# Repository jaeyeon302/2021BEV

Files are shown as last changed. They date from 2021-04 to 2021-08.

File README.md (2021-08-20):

# 2021BEV 
2021 Bachelor's degree Graduation Project, Battery Electric Vehicle  
Department of Electrical and Conputer Engineering, Seoul National University  

- Advisor : [Professor Seung-ki Sul](http://eepel.snu.ac.kr/wordpress/professor/)

## Demo Video

### [Test driving 1 : Seoul National University Campus Road (youtube video)](https://youtu.be/YFAJCFfAURw)
- Path length : 4.06Km
- Maximum slope : 7%
- Maximum speed : 30.5km/h

### [Test driving 2 : Cooling Performance test (youtube video)](https://youtu.be/0JFbmtatzrk)
- place : Seoul National University Electric Power Research Institute Parking Lot
- settled down at 44 celcius degree
- continuous maximum q-axis current (30A)

## What I made

### Inverter
- 4 layer PCB artwork (1oz 2oz 2oz 1oz) 
- Used IPM([NFAL5065L4B](https://kr.mouser.com/datasheet/2/308/1/NFAL5065L4B_D-2317681.pdf)) as the power IGBT switch
- Electrically isolated control board area from the High Power Area including IPM and DC link

### DSP - controller
- TMS320F2839D Launchpad
- Built the q-axis current regulator(PI controller with feedforward) from the scratch including resgister setting(ePWM, eCAP, GPIO, Clock, Timer)
- Implemented rotor position and speed observer to estimate right position of rotor for DQ transformation and feedforward control

## Future work
- Robust control algorithm to prevent sudden current peak from the disturbance.   
  Since there is no mechanical damper between ground and motor wheel, Bumpy road surface directly affects the controller's performance
- Hall sensor type curernt sensor removal. because the IPM already provides extra ports to measure the phase current using small register.

## Photos
- [Bicycle Photo](https://photos.app.goo.gl/71CFiTBS6PbSPb559)
- [Inverter Photo](https://photos.app.goo.gl/JQpmmjE8fstSpoiK7)

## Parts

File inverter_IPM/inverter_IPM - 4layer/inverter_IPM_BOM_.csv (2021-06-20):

Source: | G:\???滊澕?措笇\0. parkjani2 DRIVE\彀胳棳 PROJECT\?勲?濏姼\2021 臁疙攧\2021_臁疙攧_workspace(shared)\PCB - inverter\inverter_IPM\inverter_IPM - 4layer\inverter_IPM.sch
Date: | 2021-03-22 ?れ爠 11:46:58
Tool: | Eeschema (5.1.8)-1
Generator: | C:\Program Files\KiCad\bin\scripting\plugins/bom_csv_grouped_by_value_with_fp.py
Component Count: | 144
Ref | Qnty | Value | Cmp name | man# | Footprint | Description | Vendor
C1, C5, C17, C24, C33, C37, C38, C41, C44, C47, C48, C51, C53, C56, C61, | 15 | 1nF/2KV | C_Small | C1206C102KGRACTU | Capacitor_SMD:C_1206_3216Metric_Pad1.33x1.80mm_HandSolder | Unpolarized capacitor, small symbol
C2, C58, | 2 | 330uF/100V | CP1_Small | UVR2A331MHD | Capacitor_THT:CP_Radial_D12.5mm_P5.00mm | Polarized capacitor, small US symbol
C3, C59, | 2 | 1uF | C_Small | C3216X7R2A105K160AA | Capacitor_SMD:C_1206_3216Metric_Pad1.33x1.80mm_HandSolder | Unpolarized capacitor, small symbol
C4, C49, C62, C64, | 4 | 10uF/25V | C_Small | TMK212BC6106KG-T | Capacitor_SMD:C_0805_2012Metric_Pad1.18x1.45mm_HandSolder | Unpolarized capacitor, small symbol
C6, | 1 | 2.2mF | CP1 | SLPX222M100E3P3 | Capacitor_THT:CP_Radial_D30.0mm_P10.00mm_SnapIn | Polarized capacitor, US symbol
C7, C8, | 2 | 100uF/16V | CP1_Small | F931C107MCC | Capacitor_Tantalum_SMD:CP_EIA-6032-20_AVX-F_Pad2.25x2.35mm_HandSolder | Polarized capacitor, small US symbol
C9, C16, C18, C19, C20, C21, C23, C25, C27, C28, C29, C30, C32, C34, C36, C40, C43, C52, C54, C63, | 20 | 100nF | C_Small | HMF316B7104KLHT | Capacitor_SMD:C_1206_3216Metric_Pad1.33x1.80mm_HandSolder | Unpolarized capacitor, small symbol
C10, | 1 | 8.2pF | C_Small | C1206C829D5GACTU | Capacitor_SMD:C_1206_3216Metric_Pad1.33x1.80mm_HandSolder | Unpolarized capacitor, small symbol
C11, | 1 | 47uF | CP1_Small | A768KS476M1JLAE031 | Capacitor_SMD:CP_Elec_8x11.9 | Polarized capacitor, small US symbol
C12, C13, C14, | 3 | 2.2uF | C_Small | HMK325BJ225KM-P | Capacitor_SMD:C_1210_3225Metric_Pad1.33x2.70mm_HandSolder | Unpolarized capacitor, small symbol
C15, | 1 | 750pF | C_Small | C1206C751J5GACTU | Capacitor_SMD:C_1206_3216Metric_Pad1.33x1.80mm_HandSolder | Unpolarized capacitor, small symbol
C22, C31, C35, C57, C60, | 5 | 10uF/100V | C_Small | GRM32EC72A106KE05L | Capacitor_SMD:C_1210_3225Metric_Pad1.33x2.70mm_HandSolder | Unpolarized capacitor, small symbol
C26, C42, | 2 | 100uF/100V | CP1_Small | EEU-FR2A101 | Capacitor_THT:CP_Radial_D10.0mm_P5.00mm | Polarized capacitor, small US symbol
C39, | 1 | 1nF/2kV | C_Small | C1206C102KGRACTU | Capacitor_SMD:C_1206_3216Metric_Pad1.33x1.80mm_HandSolder | Unpolarized capacitor, small symbol
C45, | 1 | 10nF | C_Small | GRM2195C1H103JA01D | Capacitor_SMD:C_0805_2012Metric_Pad1.18x1.45mm_HandSolder | Unpolarized capacitor, small symbol
C46, C50, C55, | 3 | 2.2pF | C_Small | VJ0805A2R2BXACW1BC | Capacitor_SMD:C_0805_2012Metric_Pad1.18x1.45mm_HandSolder | Unpolarized capacitor, small symbol
D1, | 1 | VFT2080S-E3/4W | D_Schottky_AKA | VFT2080S-E3/4W | Package_TO_SOT_THT:TO-220-3_Vertical | Schottky diode, anode on pins 1 and 3
D2, D3, D4, D5, | 4 | SMAZ22-TP | D_Zener_Small | SMAZ22-TP | Diode_SMD:D_SMA_Handsoldering | Zener diode, small symbol
J1, | 1 | PinHeader01x03 | Conn_01x03 | PinHeader01x03 | Connector_PinHeader_2.54mm:PinHeader_1x03_P2.54mm_Vertical | Generic connector, single row, 01x03, script generated (kicad-library-utils/schlib/autogen/connector/)
J2, J3, | 2 | BR-1300C-6P | Conn_01x06 | BR-1300C-6P | j_terminal:BR-1300C-6P | Generic connector, single row, 01x06, script generated (kicad-library-utils/schlib/autogen/connector/)
J4, | 1 | MOLEX01x03 | Conn_01x03 | MOLEX_5267-03 | Connector_Molex:Molex_SPOX_5267-03A_1x03_P2.50mm_Vertical | Generic connector, single row, 01x03, script generated (kicad-library-utils/schlib/autogen/connector/)
J5, | 1 | MOLEX01x05 | Conn_01x05 | MOLEX_5267-05 | Connector_Molex:Molex_SPOX_5267-05A_1x05_P2.50mm_Vertical | Generic connector, single row, 01x05, script generated (kicad-library-utils/schlib/autogen/connector/)
J6, J8, J9, | 3 | SMA | Conn_Coaxial | SMA | Connector_Coaxial:SMA_Amphenol_132203-12_Horizontal | coaxial connector (BNC, SMA, SMB, SMC, Cinch/RCA, ...)
J7, | 1 | JST8P | Conn_01x08 | JST8P | Connector_JST:JST_VH_B8P-VH-B_1x08_P3.96mm_Vertical | Generic connector, single row, 01x08, script generated (kicad-library-utils/schlib/autogen/connector/)
J10, | 1 | MOLEX_01X05 | Conn_01x05 | molex-01x05 | Connector_Molex:Molex_SPOX_5267-05A_1x05_P2.50mm_Vertical | Generic connector, single row, 01x05, script generated (kicad-library-utils/schlib/autogen/connector/)
J11, | 1 | Hirose_HIF3BA_30PA_2.54DSA | Conn_02x15_Odd_Even |  | Connector_PinSocket_2.54mm:PinSocket_2x15_P2.54mm_Vertical | Generic connector, double row, 02x15, odd/even pin numbering scheme (row 1 odd numbers, row 2 even numbers), script generated (kicad-library-utils/schlib/autogen/connector/)
J12, | 1 | PinHeader01x02 | Conn_01x02 | pinheader 01x02 | Connector_PinHeader_2.54mm:PinHeader_1x02_P2.54mm_Vertical | Generic connector, single row, 01x02, script generated (kicad-library-utils/schlib/autogen/connector/)
J13, | 1 | HIF3 2X5 | Conn_02x05_Odd_Even | HIF3 2X5 | Connector_PinHeader_2.54mm:PinHeader_2x05_P2.54mm_Vertical | Generic connector, double row, 02x05, odd/even pin numbering scheme (row 1 odd numbers, row 2 even numbers), script generated (kicad-library-utils/schlib/autogen/connector/)
K1, | 1 | ADJH21012 | ADJH21012 | ADJH21012 | j_power_switch:Panasonic-ADJH21012-MFG | ADJH21012
L1, L3, | 2 | 4.7uH | L_Small | NRS5024T4R7MMGJV | Inductor_SMD:L_Taiyo-Yuden_NR-50xx | Inductor, small symbol
L2, | 1 | 15uH, Irms>5A | L | IHLP6767GZER150M01 | Inductor_SMD:L_Vishay_IHLP-6767 | Inductor
R1, | 1 | 442k | R_Small | HV732BTTD4423F | Resistor_SMD:R_1206_3216Metric_Pad1.30x1.75mm_HandSolder | Resistor, small symbol
R2, | 1 | 90.9k | R_Small | CRCW121090K9FKEA | Resistor_SMD:R_1210_3225Metric_Pad1.30x2.65mm_HandSolder | Resistor, small symbol
R3, | 1 | 215k | R_Small | CRCW1206215KFKEA | Resistor_SMD:R_1206_3216Metric_Pad1.30x1.75mm_HandSolder | Resistor, small symbol
R4, | 1 | 205k | R_Small | CRCW1206205KFKEA | Resistor_SMD:R_1206_3216Metric_Pad1.30x1.75mm_HandSolder | Resistor, small symbol
R5, | 1 | 44.2k | R_Small | ERA-8AEB4422V | Resistor_SMD:R_1206_3216Metric_Pad1.30x1.75mm_HandSolder | Resistor, small symbol
R6, | 1 | 12.1k | R_Small | ERA-8AEB1212V | Resistor_SMD:R_1206_3216Metric_Pad1.30x1.75mm_HandSolder | Resistor, small symbol
R7, R11, R15, R17, R20, R22, R23, | 7 | 100 | R_Small | CHP0805AFX-1000ELF | Resistor_SMD:R_0805_2012Metric_Pad1.20x1.40mm_HandSolder | Resistor, small symbol
R8, R9, R10, R12, R13, R14, R19, R34, R35, R36, R37, R38, R39, | 13 | 1k | R_Small | CMP2010AFX-1001ELF | Resistor_SMD:R_2010_5025Metric_Pad1.40x2.65mm_HandSolder | Resistor, small symbol
R16, | 1 | 5k | R_Small | CRCW08055K00FKTA | Resistor_SMD:R_0805_2012Metric_Pad1.20x1.40mm_HandSolder | Resistor, small symbol
R18, | 1 | 24 | R_Small | RK73H2ATTD24R0F | Resistor_SMD:R_0805_2012Metric_Pad1.20x1.40mm_HandSolder | Resistor, small symbol
R21, | 1 | 249 | R_Small | RK73H2ATTD2490F | Resistor_SMD:R_0805_2012Metric_Pad1.20x1.40mm_HandSolder | Resistor, small symbol
R24, R27, R28, R31, | 4 | 24k | R_Small | CR1206-JW-243ELF | Resistor_SMD:R_1206_3216Metric_Pad1.30x1.75mm_HandSolder | Resistor, small symbol
R25, R26, R29, R30, | 4 | 12k | R_Small | CRCW120612K0FKEAC | Resistor_SMD:R_1206_3216Metric_Pad1.30x1.75mm_HandSolder | Resistor, small symbol
R32, | 1 | 1M | R_Small | ERA-8AED105V | Resistor_SMD:R_1206_3216Metric_Pad1.30x1.75mm_HandSolder | Resistor, small symbol
R33, | 1 | 68k | R_Small | CRCW120668K0FKEAHP | Resistor_SMD:R_1206_3216Metric_Pad1.30x1.75mm_HandSolder | Resistor, small symbol
S1, | 1 | EG2219 | EG2219 | EG2219 | j_switch:SW_EG2219
U1, | 1 | PDQE10-Q48-S5-D | PDQE10-Q48-S5-D | PDQE10-Q48-S5-D | PDQE10:CONV_PDQE10-Q48-S5-D
U2, | 1 | SPX1587AT-3.3 | AZ1117-5.0 | SPX1587AT-3.3 | Package_TO_SOT_SMD:TO-263-3_TabPin4 | 1A 20V Fixed LDO Linear Regulator, 5.0V, SOT-89/SOT-223/TO-220/TO-252/TO-263
U3, | 1 | LAUNCHXL_F28379D | LAUNCHXL_F28379D | LAUNCHPAD_F28379D | j_modules:LAUNCHXL_F28379D
U4, | 1 | TPS54560BDDA | TPS54560BDDA | TPS54560BDDA | j_regulator_switching:NOPB
U5, | 1 | NFAL5065L4B-New_Library | NFAL5065L4B-New_Library | NFAL5065L4B | j_IPM:NFAL5065L4B
U6, U7, U8, U10, U11, U12, U13, | 7 | TLP2748 | TLP2748 | TLP2748 | Package_SO:SO-6L_10x3.84mm_P1.27mm | 10-Mbps inverting photocouple,5 kVrms, 4.5 - 30 Vdd, push-pull output, SO-6L
U9, | 1 | PDQE10-Q48-D15-D | PDQE10-Q48-D15-D | PDQE10-Q48-D15-D | PDQE10:CONV_PDQE10-Q48-D15-D
U14, U16, | 2 | LM358 | LM358 | LM358 | Package_SO:SO-8_3.9x4.9mm_P1.27mm | opamp
U15, U17, U18, | 3 | wcs1800 | wcs1800 | wcs1800 | j_current_sensor:wcs1x00-xxxx

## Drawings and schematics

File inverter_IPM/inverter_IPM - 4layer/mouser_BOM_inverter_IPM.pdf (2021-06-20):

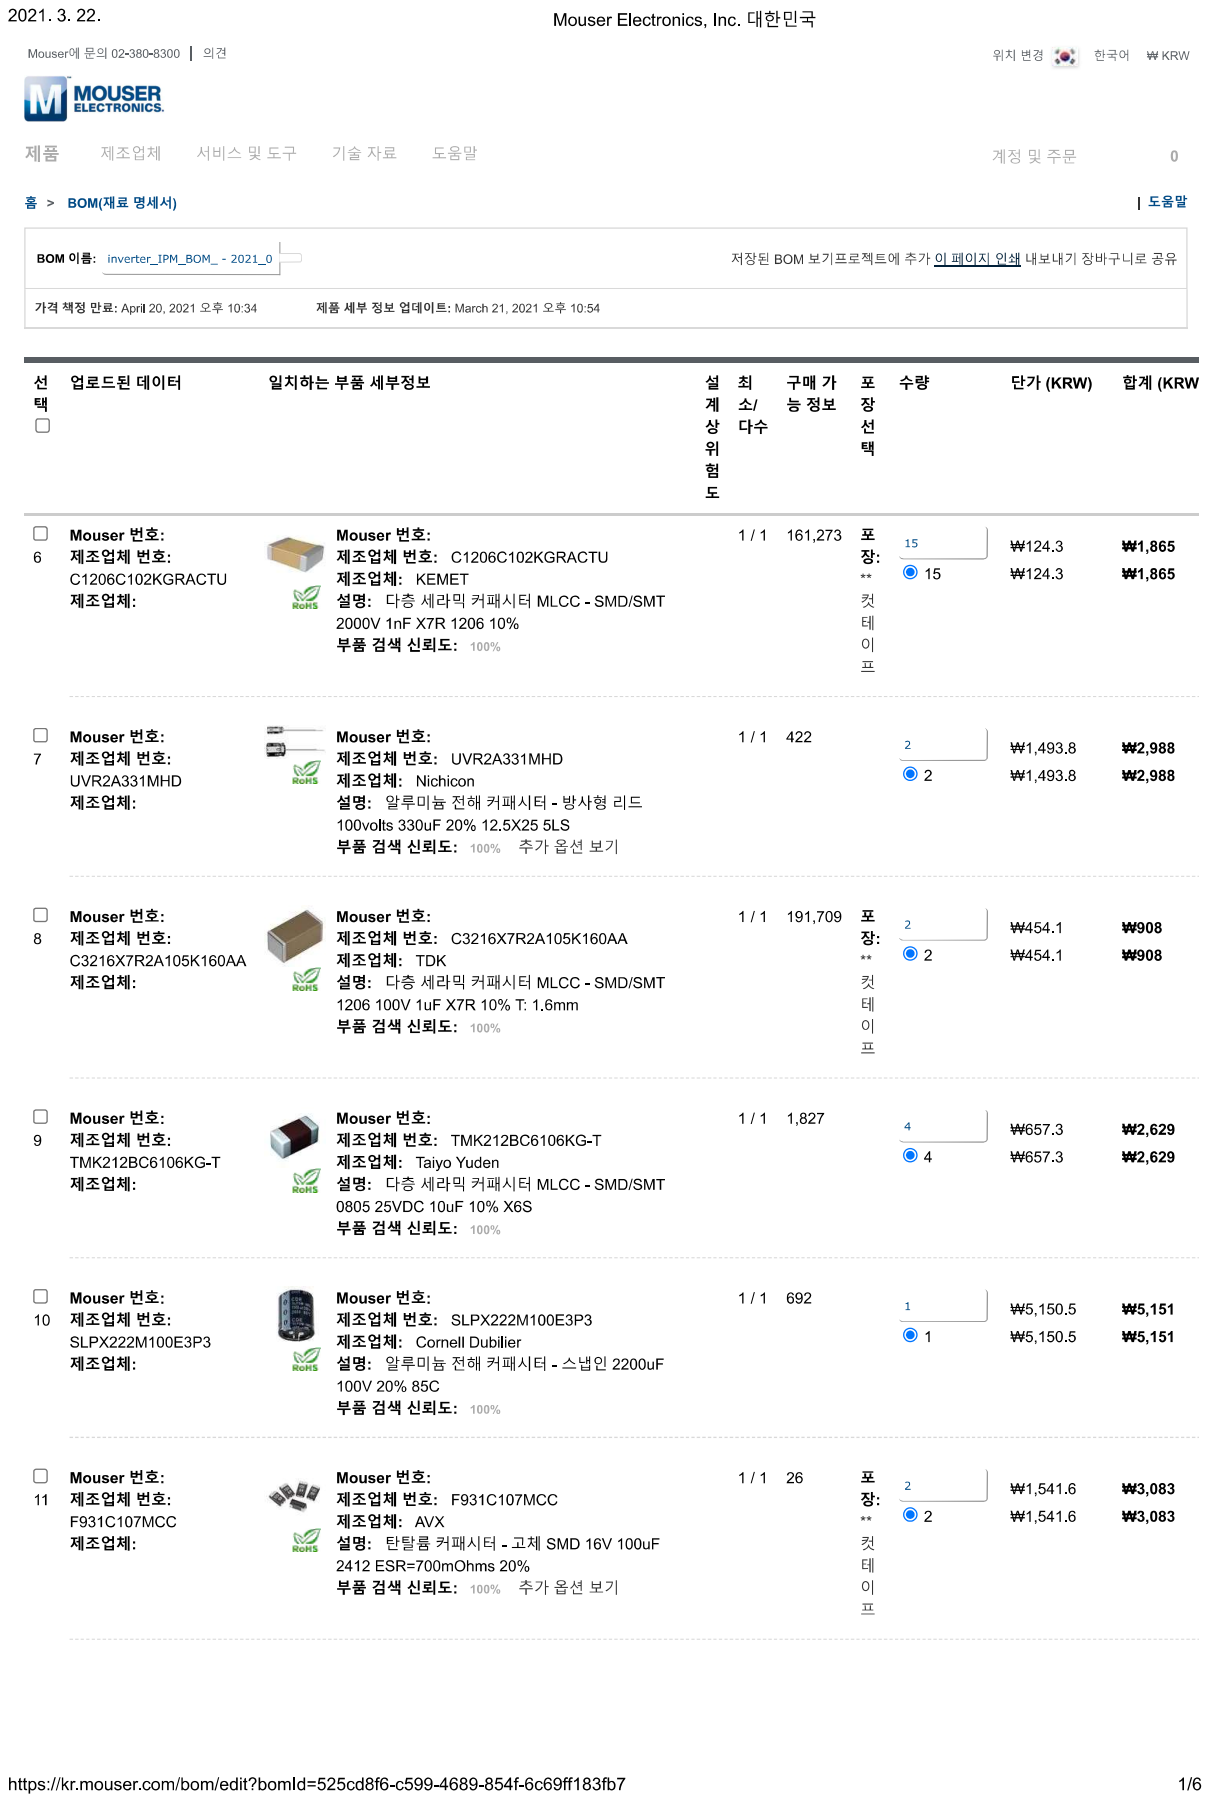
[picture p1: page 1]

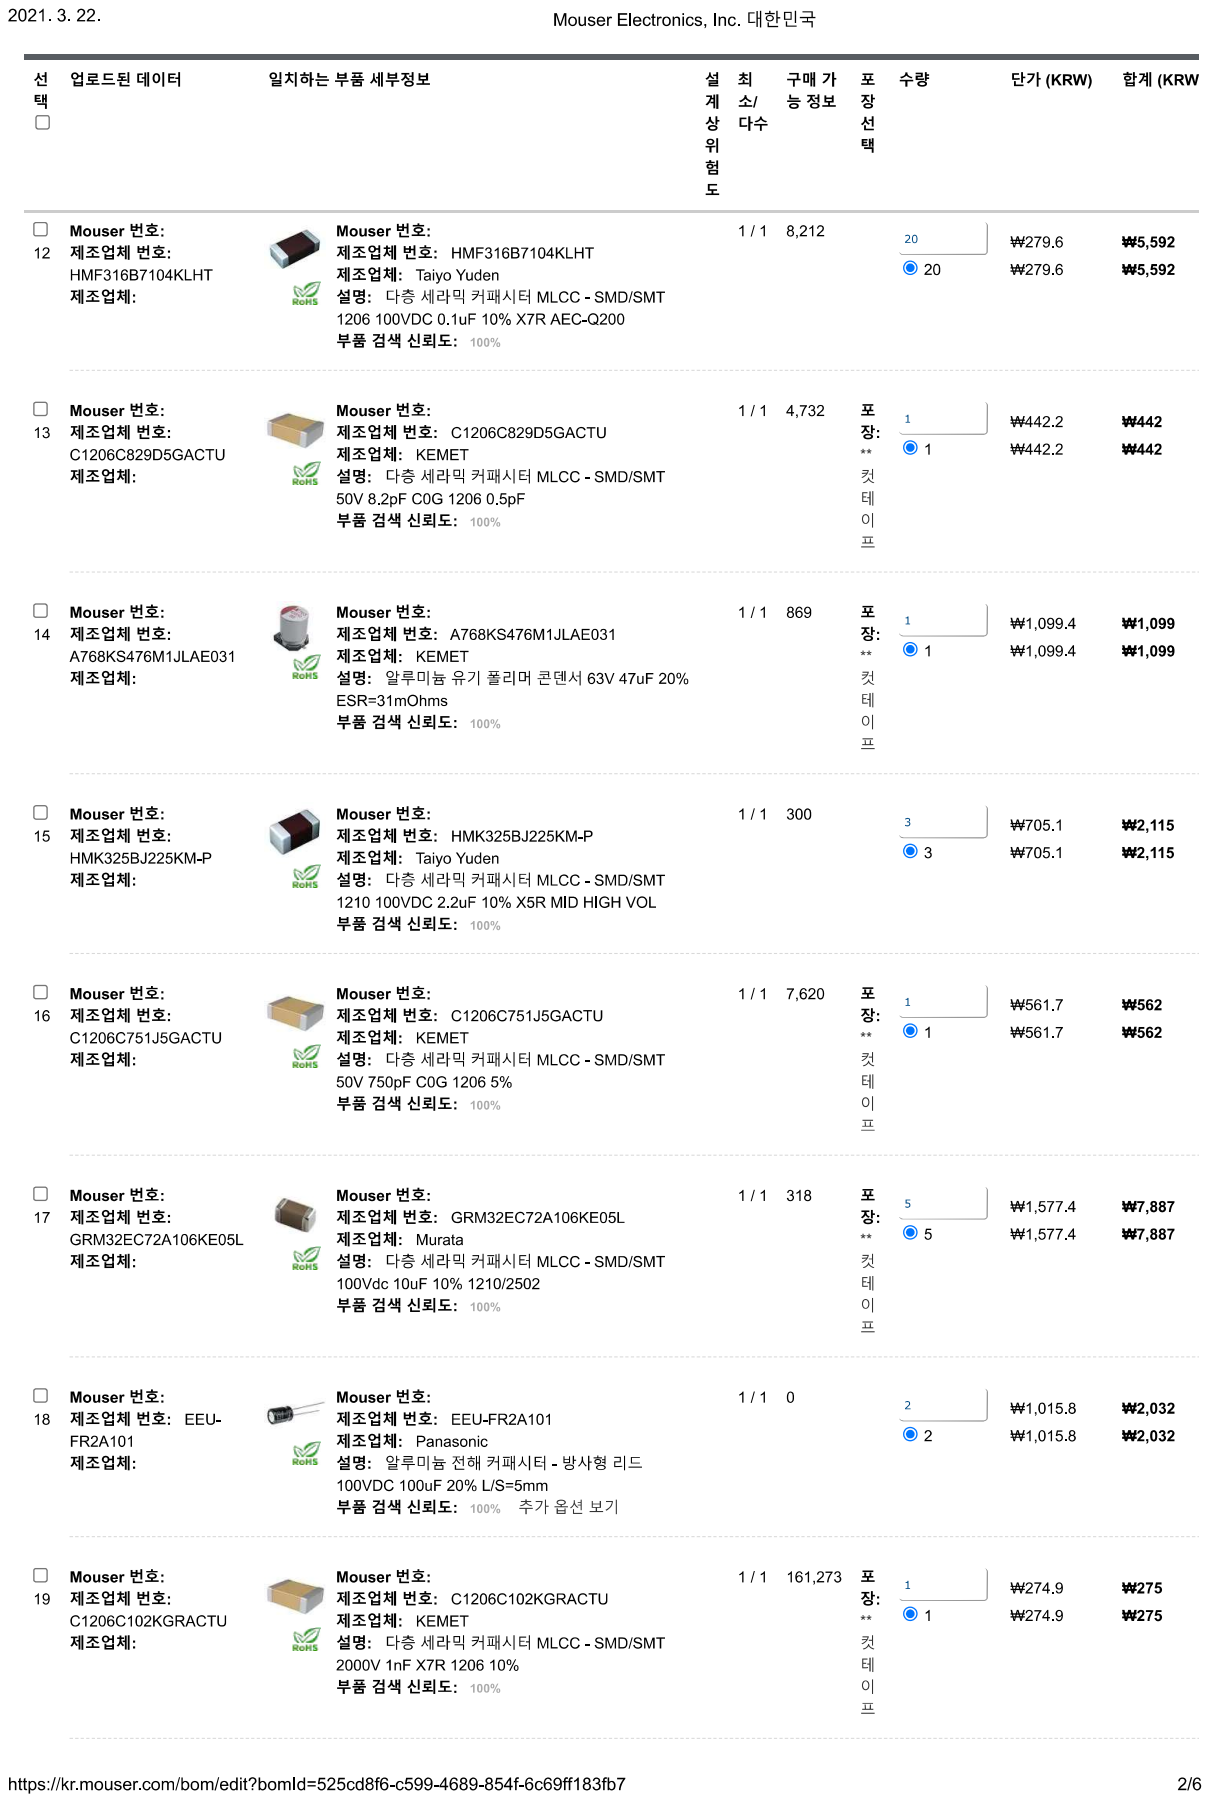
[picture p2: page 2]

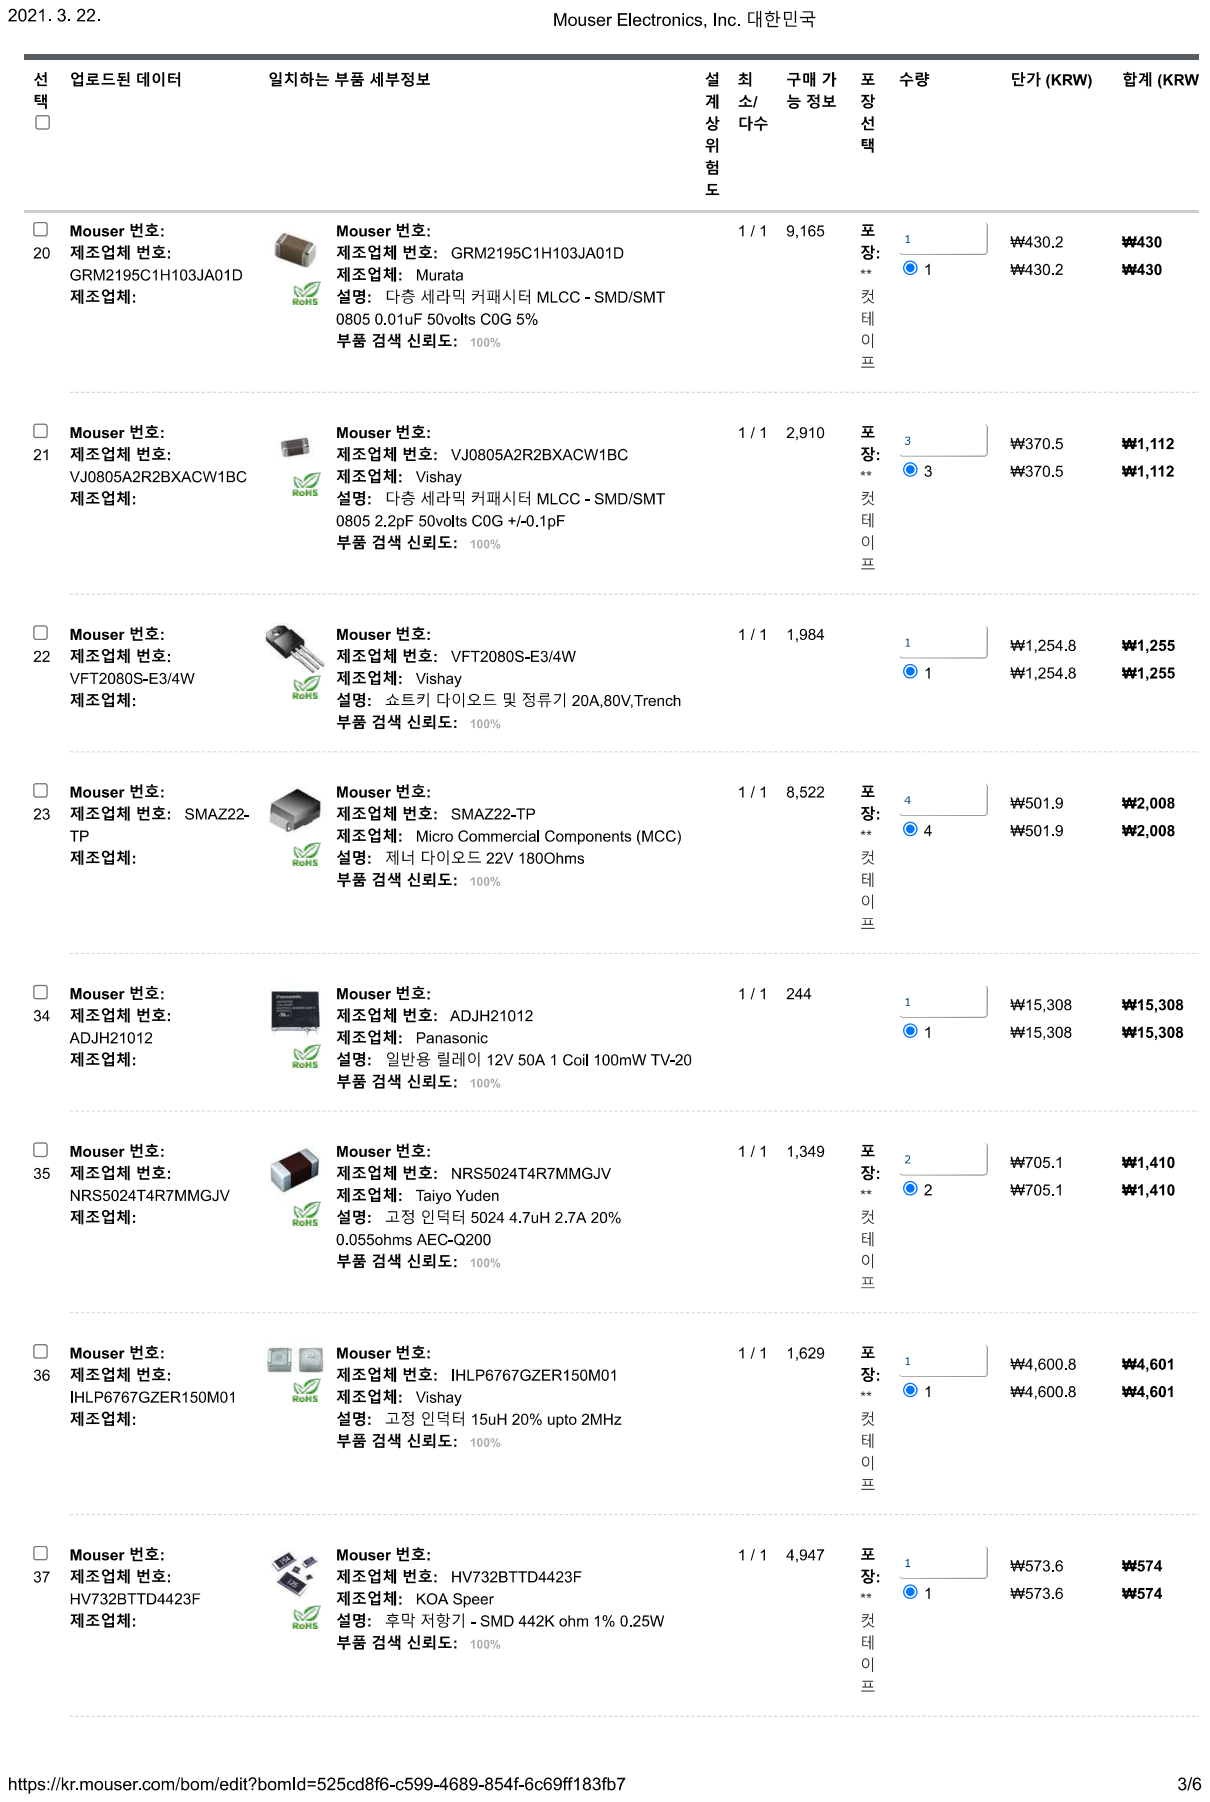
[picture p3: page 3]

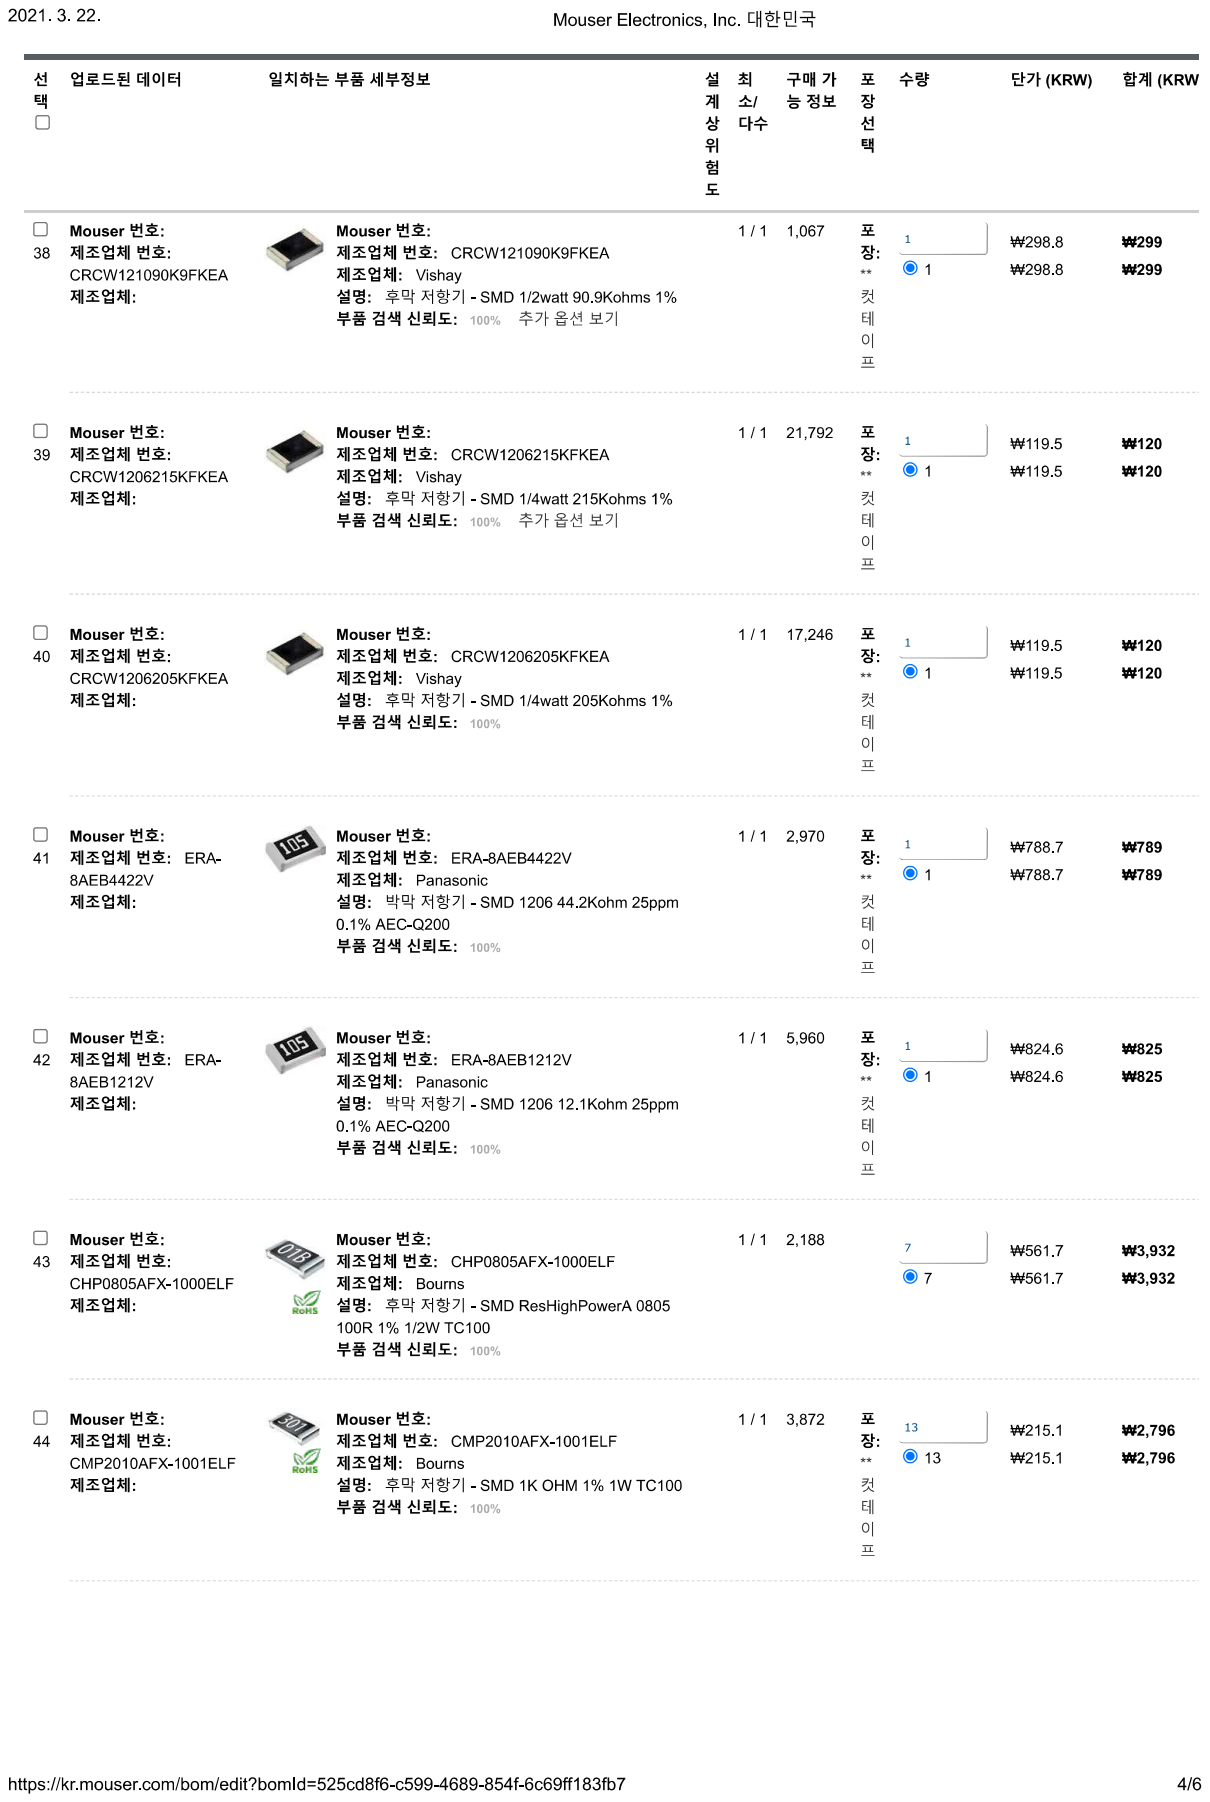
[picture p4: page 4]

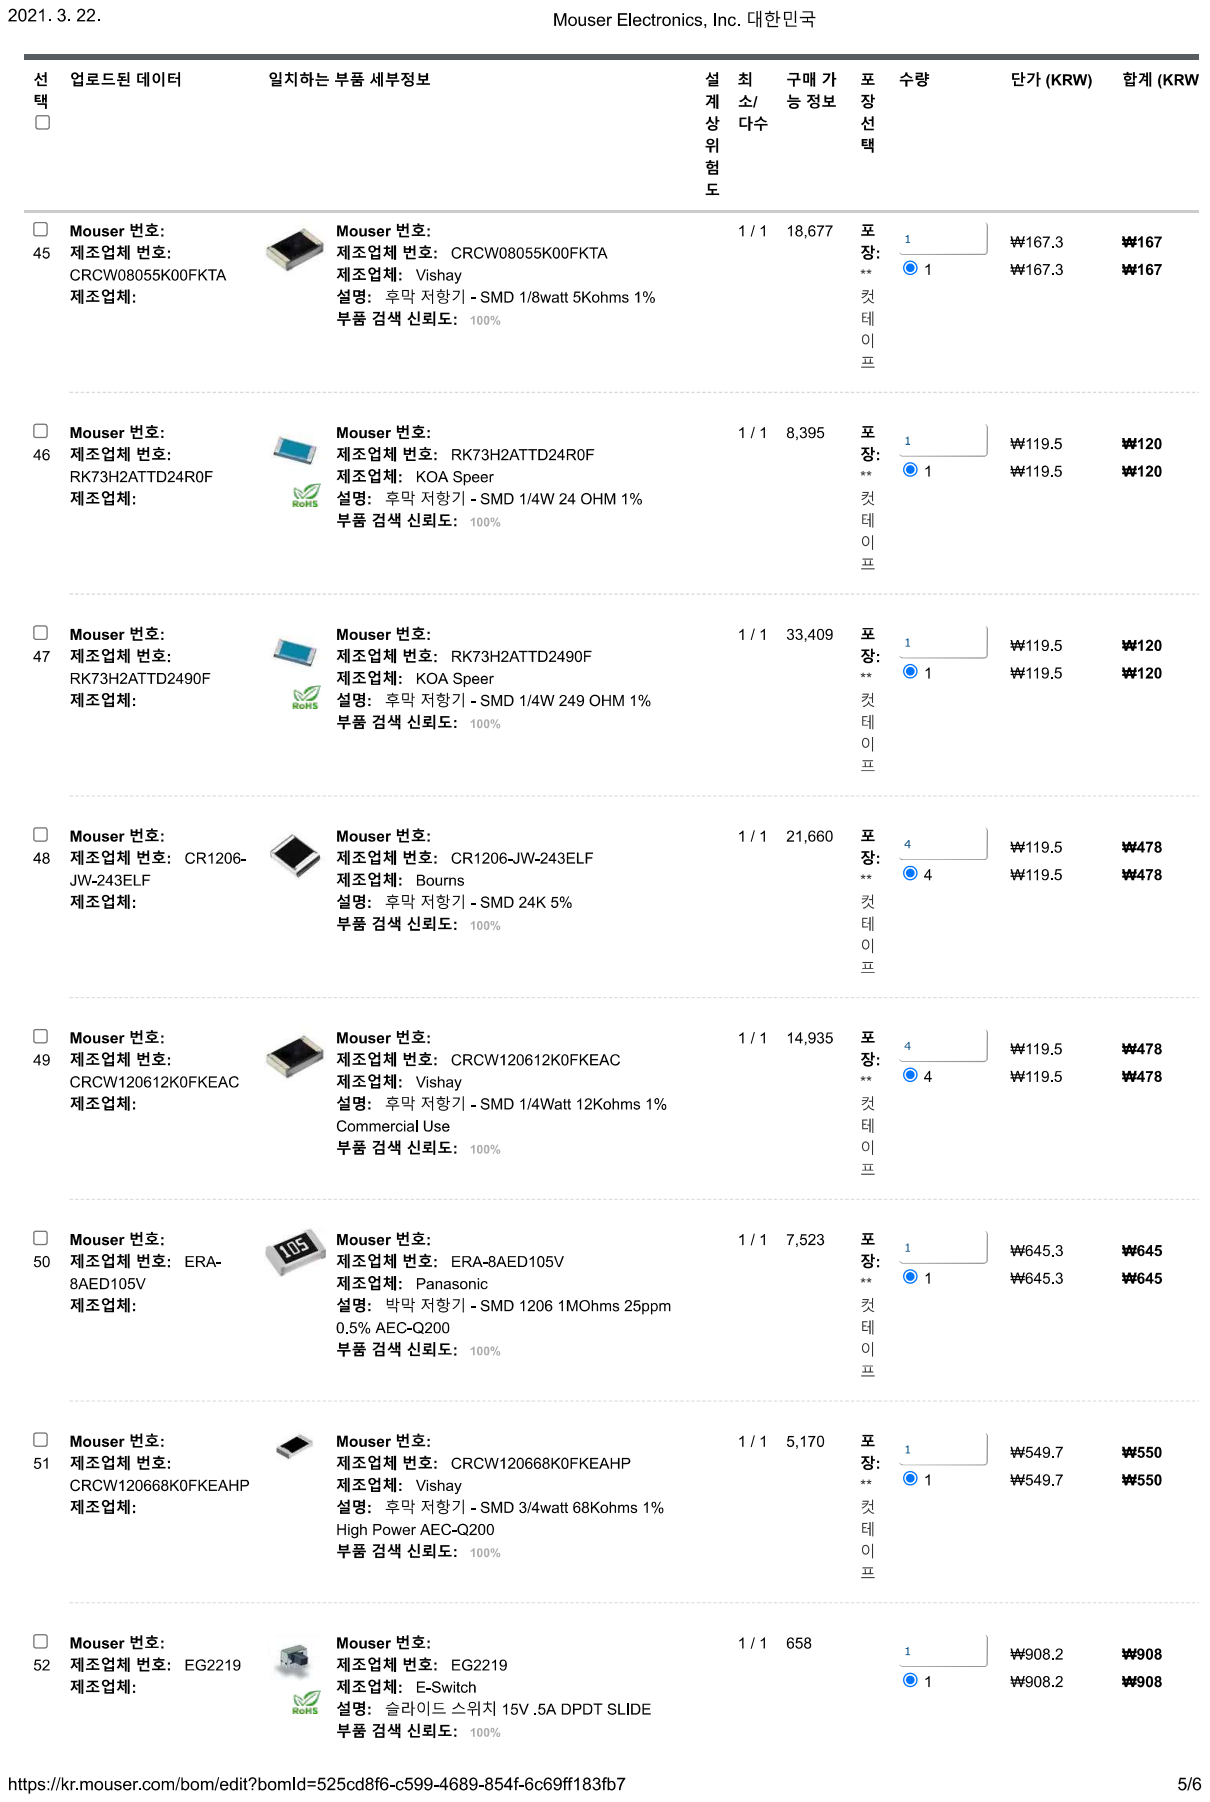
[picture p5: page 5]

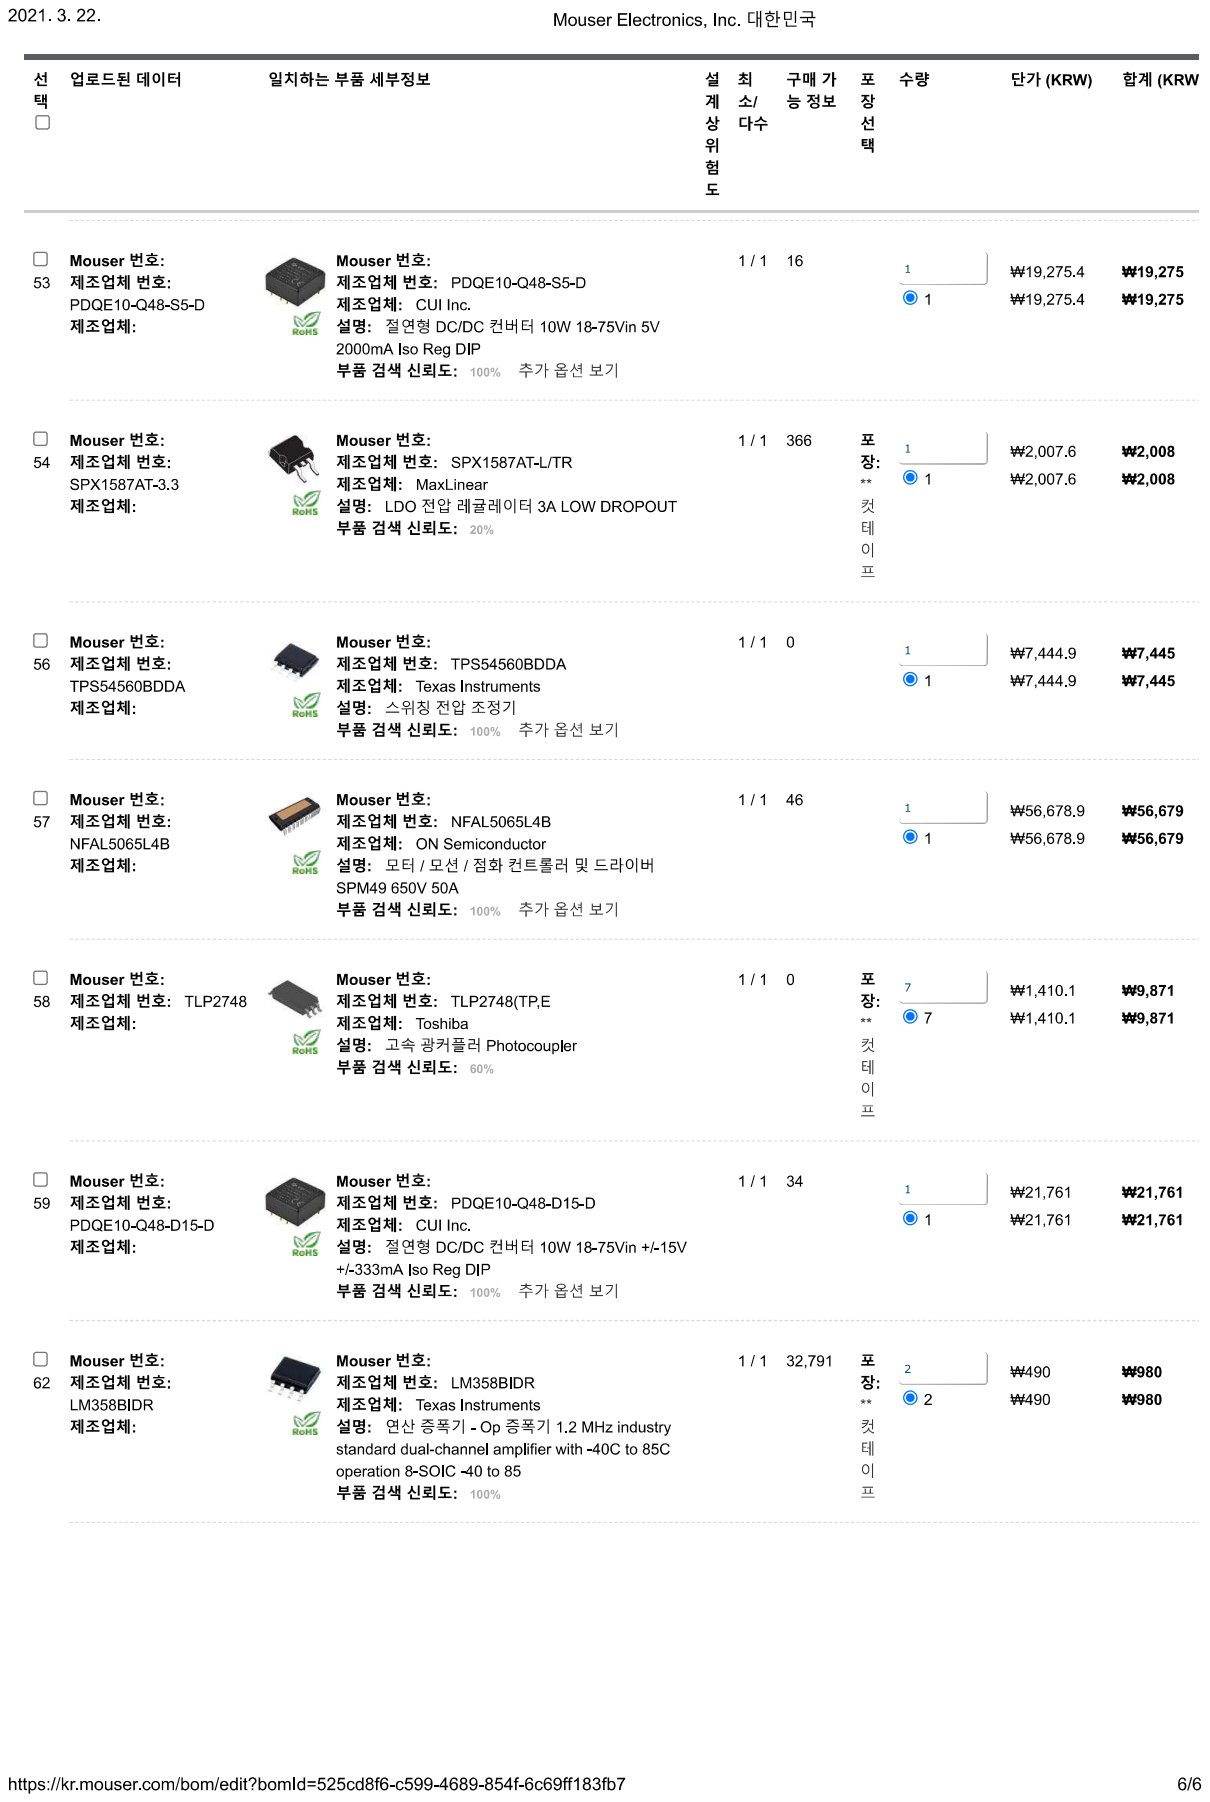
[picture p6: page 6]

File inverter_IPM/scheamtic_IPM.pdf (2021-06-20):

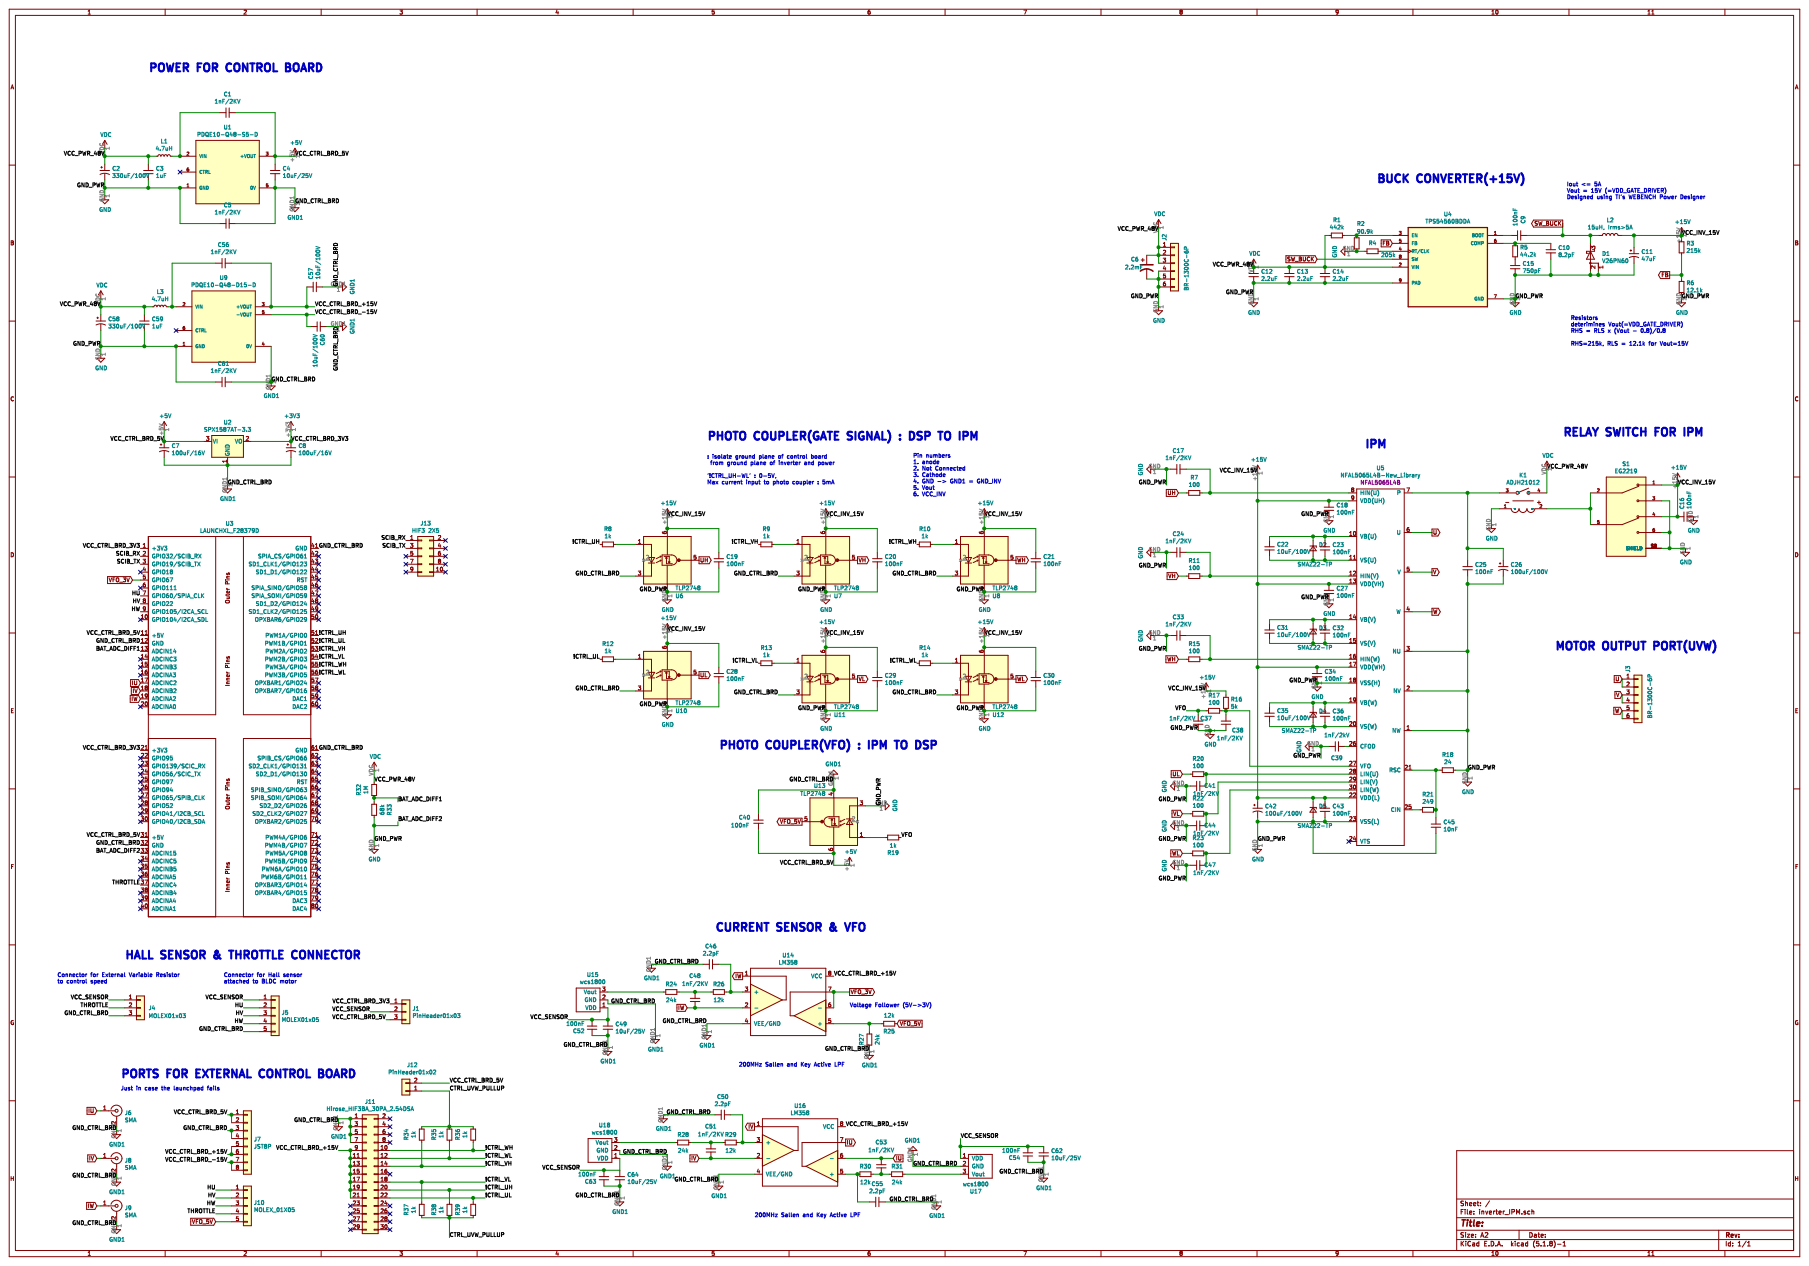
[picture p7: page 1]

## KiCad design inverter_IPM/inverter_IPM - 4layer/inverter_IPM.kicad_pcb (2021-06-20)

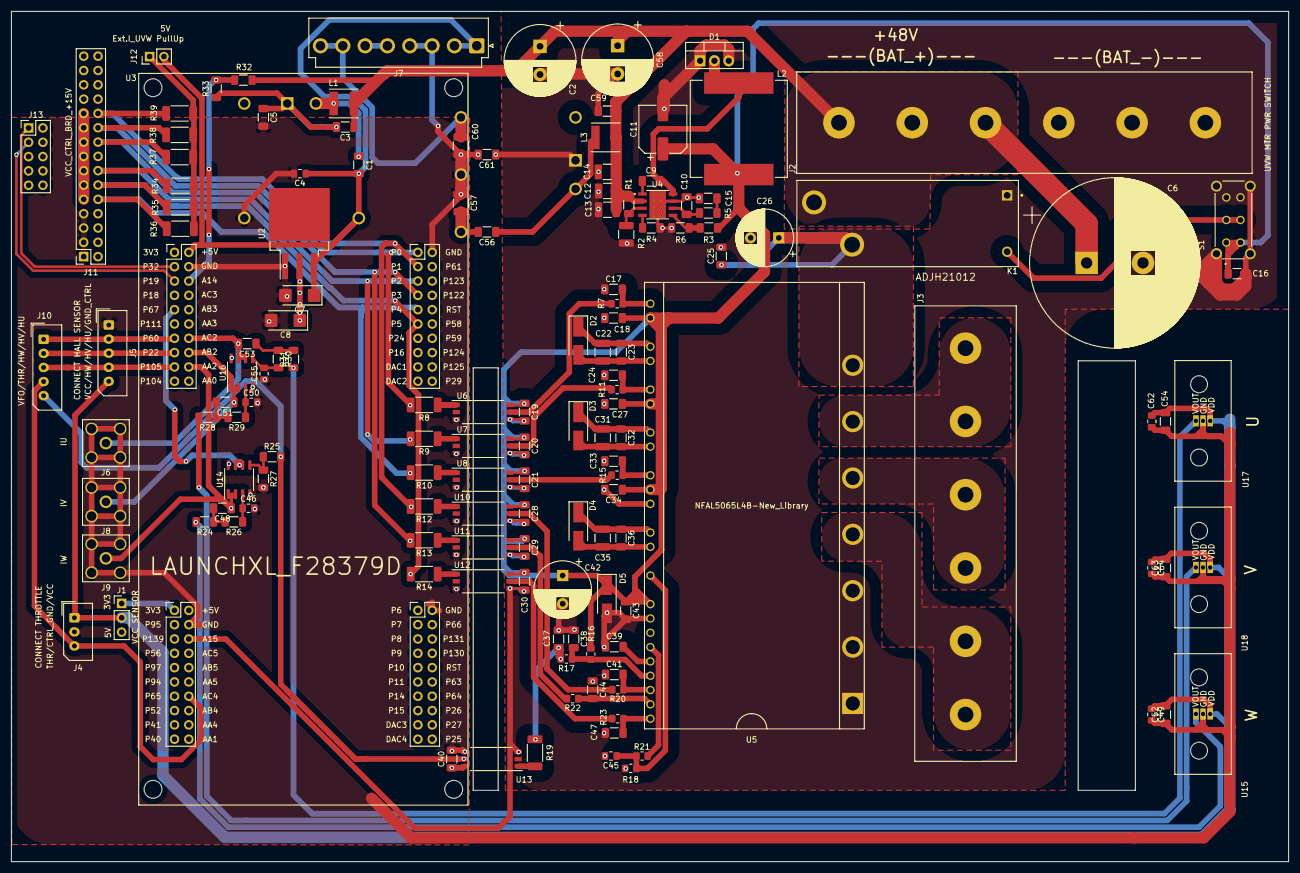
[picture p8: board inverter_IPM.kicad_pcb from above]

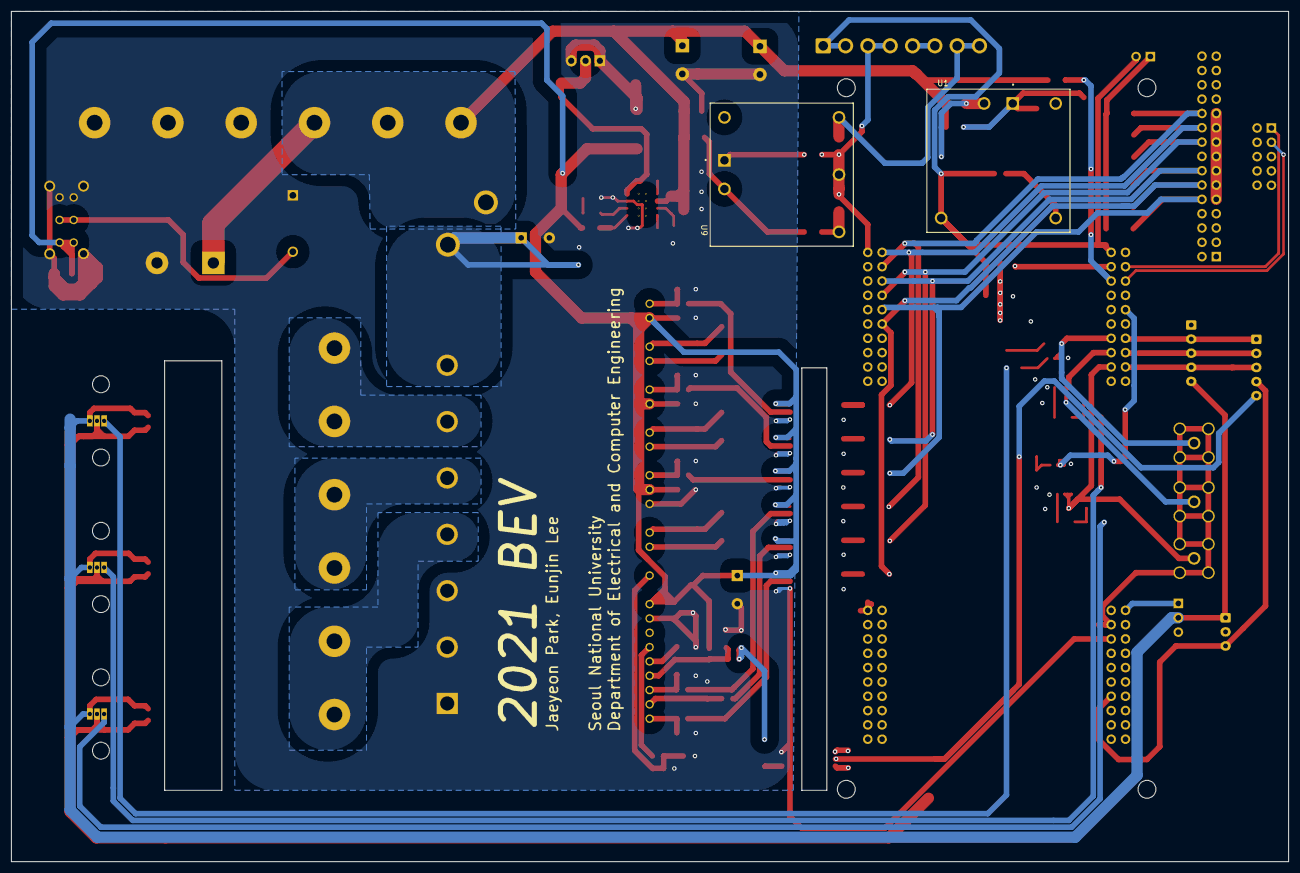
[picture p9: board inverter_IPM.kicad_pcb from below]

Board: 4 copper layers, 226.6 x 150.8 mm, 144 parts (2 on the bottom side), 82 nets.

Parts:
C1, C5, C17, C24, C33, C37, C38, C41, C44, C47, C48, C51, C53, C56, C61: 1nF/2KV; C_1206_3216Metric_Pad1.33x1.80mm_HandSolder
C2, C58: 330uF/100V; CP_Radial_D12.5mm_P5.00mm
C3, C59: 1uF; C_1206_3216Metric_Pad1.33x1.80mm_HandSolder
C4, C49, C62, C64: 10uF/25V; C_0805_2012Metric_Pad1.18x1.45mm_HandSolder
C6: 2.2mF; CP_Radial_D30.0mm_P10.00mm_SnapIn
C7, C8: 100uF/16V; CP_EIA-6032-20_AVX-F_Pad2.25x2.35mm_HandSolder
C9, C16, C18, C19, C20, C21, C23, C25, C27, C28, C29, C30, C32, C34, C36, C40, C43, C52, C54, C63: 100nF; C_1206_3216Metric_Pad1.33x1.80mm_HandSolder
C10: 8.2pF; C_1206_3216Metric_Pad1.33x1.80mm_HandSolder
C11: 47uF; CP_Elec_8x11.9
C12, C13, C14: 2.2uF; C_1210_3225Metric_Pad1.33x2.70mm_HandSolder
C15: 750pF; C_1206_3216Metric_Pad1.33x1.80mm_HandSolder
C22, C31, C35, C57, C60: 10uF/100V; C_1210_3225Metric_Pad1.33x2.70mm_HandSolder
C26, C42: 100uF/100V; CP_Radial_D10.0mm_P5.00mm
C39: 1nF/2kV; C_1206_3216Metric_Pad1.33x1.80mm_HandSolder
C45: 10nF; C_0805_2012Metric_Pad1.18x1.45mm_HandSolder
C46, C50, C55: 2.2pF; C_0805_2012Metric_Pad1.18x1.45mm_HandSolder
D1: VFT2080S-E3/4W; TO-220-3_Vertical
D2, D3, D4, D5: SMAZ22-TP; D_SMA_Handsoldering
J1: PinHeader01x03; PinHeader_1x03_P2.54mm_Vertical
J2, J3: BR-1300C-6P
J4: MOLEX01x03; Molex_SPOX_5267-03A_1x03_P2.50mm_Vertical
J5: MOLEX01x05; Molex_SPOX_5267-05A_1x05_P2.50mm_Vertical
J6, J8, J9: SMA; SMA_Amphenol_132203-12_Horizontal
J7: JST8P; JST_VH_B8P-VH-B_1x08_P3.96mm_Vertical
J10: MOLEX_01X05; Molex_SPOX_5267-05A_1x05_P2.50mm_Vertical
J11: Hirose_HIF3BA_30PA_2.54DSA; PinSocket_2x15_P2.54mm_Vertical
J12: PinHeader01x02; PinHeader_1x02_P2.54mm_Vertical
J13: HIF3 2X5; PinHeader_2x05_P2.54mm_Vertical
K1: ADJH21012; Panasonic-ADJH21012-MFG
L1, L3: 4.7uH; L_Taiyo-Yuden_NR-50xx
L2: 15uH, Irms>5A; L_Vishay_IHLP-6767
R1: 442k; R_1206_3216Metric_Pad1.30x1.75mm_HandSolder
R2: 90.9k; R_1210_3225Metric_Pad1.30x2.65mm_HandSolder
R3: 215k; R_1206_3216Metric_Pad1.30x1.75mm_HandSolder
R4: 205k; R_1206_3216Metric_Pad1.30x1.75mm_HandSolder
R5: 44.2k; R_1206_3216Metric_Pad1.30x1.75mm_HandSolder
R6: 12.1k; R_1206_3216Metric_Pad1.30x1.75mm_HandSolder
R7, R11, R15, R17, R20, R22, R23: 100; R_0805_2012Metric_Pad1.20x1.40mm_HandSolder
R8, R9, R10, R12, R13, R14, R19, R34, R35, R36, R37, R38, R39: 1k; R_2010_5025Metric_Pad1.40x2.65mm_HandSolder
R16: 5k; R_0805_2012Metric_Pad1.20x1.40mm_HandSolder
R18: 24; R_0805_2012Metric_Pad1.20x1.40mm_HandSolder
R21: 249; R_0805_2012Metric_Pad1.20x1.40mm_HandSolder
R24, R27, R28, R31: 24k; R_1206_3216Metric_Pad1.30x1.75mm_HandSolder
R25, R26, R29, R30: 12k; R_1206_3216Metric_Pad1.30x1.75mm_HandSolder
R32: 1M; R_1206_3216Metric_Pad1.30x1.75mm_HandSolder
R33: 68k; R_1206_3216Metric_Pad1.30x1.75mm_HandSolder
S1: EG2219; SW_EG2219
U1: PDQE10-Q48-S5-D; CONV_PDQE10-Q48-S5-D
U2: SPX1587AT-3.3; TO-263-3_TabPin4
U3: LAUNCHXL_F28379D
U4: TPS54560BDDA; NOPB
U5: NFAL5065L4B-New_Library; NFAL5065L4B
U6, U7, U8, U10, U11, U12, U13: TLP2748; SO-6L_10x3.84mm_P1.27mm
U9: PDQE10-Q48-D15-D; CONV_PDQE10-Q48-D15-D
U14, U16: LM358; SO-8_3.9x4.9mm_P1.27mm
U15, U17, U18: wcs1800; wcs1x00-xxxx

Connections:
+3V3: C8.1, J1.1, U2.2, U3.1, U3.21
+5V: C1.2, C4.1, C7.1, C40.1, J1.3, J7.1, J7.2, J12.2, U1.3, U2.3, U3.11, U3.31, U13.6
+15V: C11.1, C16.1, C18.1, C19.1, C20.1, C21.1, C27.1, C28.1, C29.1, C30.1, C34.1, C42.1, C43.1, D5.1, L2.2, R3.2, R16.1, S1.1, S1.4, U5.9, U5.13, U5.17, U5.22, U6.6, U7.6, U8.6, U10.6, U11.6, U12.6
/!CTRL_UH: J11.20, R8.2, R38.1, U3.51
/!CTRL_UL: J11.22, R12.2, R39.1, U3.52
/!CTRL_VH: J11.14, R9.2, R34.2, U3.53
/!CTRL_VL: J11.18, R13.2, R37.1, U3.54
/!CTRL_WH: J11.10, R10.2, R36.2, U3.55
/!CTRL_WL: J11.12, R14.2, R35.2, U3.56
/BAT_ADC_DIFF1: R32.2, R33.2, U3.13
/CTRL_UVW_PULLUP: J12.1, R34.1, R35.1, R36.1, R37.2, R38.2, R39.2
/HU: J5.2, J10.1, U3.7
/HV: J5.3, J10.2, U3.8
/HW: J5.4, J10.3, U3.9
/SCIB_RX: J13.1, U3.2
/SCIB_TX: J13.3, U3.3
/THROTTLE: J4.3, J10.4, U3.37
/VCC_CTRL_BRD_+15V: C56.2, C57.2, J7.5, J7.6, J11.9, J11.11, J11.13, J11.15, J11.17, J11.19, J11.21, U9.3, U14.8, U16.8
/VCC_CTRL_BRD_-15V: C60.1, J7.7, J7.8, U9.5
/VCC_SENSOR: C49.1, C52.2, C54.2, C62.1, C63.2, C64.1, J1.2, J4.1, J5.5, U15.1, U17.1, U18.1
/VFO: C37.2, R17.2, R19.2
FB: R3.1, R6.2, U4.5
GND: C2.2, C3.2, C5.1, C6.2, C10.2, C11.2, C12.2, C13.2, C14.2, C15.2, C16.2, C17.1, C18.2, C19.2, C20.2, C21.2, C24.1, C25.2, C26.2, C27.2, C28.2, C29.2, C30.2, C33.1, C34.2, C37.1, C38.1, C39.1, C41.1, C42.2, C43.2, C44.1, C45.2, C47.1, C58.2, C59.2, C61.1, D1.1, D1.3, D5.2, J2.4, J2.5, J2.6, K1.1, R2.2, R4.1, R6.1, R18.1, R33.1, S1.3, S1.6, S1.S1, S1.S2, S1.S3, S1.S4, U1.1, U3.33, U4.7, U4.9, U5.1, U5.2, U5.3, U5.18, U5.23, U6.4, U7.4, U8.4, U9.1, U10.4, U11.4, U12.4, U13.3
GND1: C4.2, C5.2, C7.2, C8.2, C40.2, C46.2, C49.2, C50.2, C52.1, C54.1, C55.1, C57.1, C60.2, C61.2, C62.2, C63.1, C64.2, J4.2, J5.1, J6.2, J7.3, J7.4, J8.2, J9.2, J11.1, J11.3, J11.5, J11.7, R27.2, U1.5, U2.1, U3.12, U3.32, U3.41, U3.61, U6.3, U7.3, U8.3, U9.4, U10.3, U11.3, U12.3, U13.4, U14.4, U15.2, U16.4, U17.2, U18.2
IU: C53.2, J6.1, U3.17, U16.6, U16.7
IV: C51.1, J8.1, U3.18, U16.1, U16.2
IW: C48.1, J9.1, U3.19, U14.1, U14.2
unnamed: C1.1, L1.2, U1.2
unnamed: C9.1, U4.1
unnamed: C10.1, R5.2, U4.6
unnamed: C15.1, R5.1
unnamed: C17.2, R7.1, U5.8
unnamed: C22.1, C23.2, D2.2, U5.11
unnamed: C22.2, C23.1, D2.1, U5.10
unnamed: C24.2, R11.1, U5.12
unnamed: C25.1, C26.1, K1.3, U5.7
unnamed: C31.1, C32.2, D3.2, U5.15
unnamed: C31.2, C32.1, D3.1, U5.14
unnamed: C33.2, R15.1, U5.16
unnamed: C35.1, C36.2, D4.2, U5.20
unnamed: C35.2, C36.1, D4.1, U5.19
unnamed: C38.2, R16.2, R17.1, U5.27
unnamed: C39.2, U5.26
unnamed: C41.2, R20.1, U5.28
unnamed: C44.2, R22.1, U5.29
unnamed: C45.1, R18.2, R21.1, U5.21
unnamed: C46.1, R26.1, U14.3
unnamed: C47.2, R23.1, U5.30
unnamed: C48.2, R24.1, R26.2
unnamed: C50.1, R29.1, U16.3
unnamed: C51.2, R28.1, R29.2
unnamed: C53.1, R30.1, R31.2
unnamed: C55.2, R30.2, U16.5
unnamed: C56.1, L3.2, U9.2
unnamed: K1.2, S1.2, S1.5
unnamed: R1.1, R2.1, U4.3
unnamed: R4.2, U4.4
unnamed: R8.1, U6.1
unnamed: R9.1, U7.1
unnamed: R10.1, U8.1
unnamed: R12.1, U10.1
unnamed: R13.1, U11.1
unnamed: R14.1, U12.1
unnamed: R19.1, U13.1
unnamed: R21.2, U5.25
unnamed: R24.2, U15.3
unnamed: R25.1, R27.1, U14.5
unnamed: R28.2, U18.3
unnamed: R31.1, U17.3
SW_BUCK: C9.2, D1.2, L2.1, U4.8
U: J3.1, J3.2, U5.6
UH: R7.2, U6.5
UL: R20.2, U10.5
V: J3.3, J3.4, U5.5
VDC: C2.1, C3.1, C6.1, C12.1, C13.1, C14.1, C58.1, C59.1, J2.1, J2.2, J2.3, K1.4, L1.1, L3.1, R1.2, R32.1, U4.2
VFO_3V: U3.5, U14.6, U14.7
VFO_5V: J10.5, R25.2, U13.5
VH: R11.2, U7.5
VL: R22.2, U11.5
W: J3.5, J3.6, U5.4
WH: R15.2, U8.5
WL: R23.2, U12.5

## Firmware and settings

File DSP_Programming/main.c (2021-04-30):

#include <F28x_Project.h>

/**
 * main.c
 *
 * 2021 BEV
 * Author: Jaeyeon Park
 *
 */
#include "controller.h"
#define INITIAL_DELAY 10000000 // MICROSECONDS
#define TIMER0_DURATION 1000000 // microseconds
#define NUM_OF_RECORDS 300
float32 testcurrentD=0;
float32 testcurrentQ=0;
//float32 angles[NUM_OF_RECORDS];
//float32 samples[NUM_OF_RECORDS];
//float32 phase_currents[NUM_OF_RECORDS];
//float32 d_currents[NUM_OF_RECORDS];
//float32 q_currents[NUM_OF_RECORDS];
Uint32 i = 0;
Uint32 record = 0;

interrupt void timer0_debugging_isr(){
    CpuTimer0.InterruptCount++;
    test_Idq_update(testcurrentD,testcurrentQ);
   if(record){
       if(i < NUM_OF_RECORDS){
           //angles[i] = get_angle_observer().angle;//hall_sensor_get_E_angle_rad();//get_hall_state().angle_E_rad;
           //phase_currents[i] = get_3phase_currents()[phaseU];
           //d_currents[i] = get_dqr_currents()[0]; // 0: d-axis, 1: q-axis
           //q_currents[i] = get_dqr_currents()[1];
           i++;
       }
   }

    GpioDataRegs.GPATOGGLE.bit.GPIO31 = 1; //flip the led state0
    PieCtrlRegs.PIEACK.all = PIEACK_GROUP1; // clear PIEACK.1 == PIEACK switch closed
}


int main(void){
    InitSysCtrl();
    InitGpio();

    DINT;
    InitPieCtrl();
    IER = 0x0000;
    IFR = 0x0000;
    InitPieVectTable();

    DELAY_US(INITIAL_DELAY);
    GpioDataRegs.GPATOGGLE.bit.GPIO31 = 1;

    Ready_controller();
    EALLOW;

    /* SETTING TIMER0 FOR DEBUGGING */
    // enable clock for timers
    // debugging timer
    // GPIO SETUP
    // BUILT IN LED
    GpioCtrlRegs.GPAGMUX2.bit.GPIO31 = 0;
    GpioCtrlRegs.GPAMUX2.bit.GPIO31 = 0;
    GpioCtrlRegs.GPADIR.bit.GPIO31 = 1; // GPIO FOR OUTPUT

    CpuSysRegs.PCLKCR0.bit.CPUTIMER0 = 1;
    CpuSysRegs.PCLKCR0.bit.CPUTIMER1 = 1;
    InitCpuTimers(); // initialize global variable CpuTimer0, CpuTimer1, CpuTimer2
    ConfigCpuTimer(&CpuTimer0,200, TIMER0_DURATION); // timer, 200MHz(PLL CLK),
    IER |= (M_INT13 | M_INT1); // M_INT13 = CPU TIMER1 interrupt, M_INT1 = PIE1 (to enable timer0 interrupt)

    PieCtrlRegs.PIECTRL.bit.ENPIE = 1; // set total PIE Enable Register
    PieCtrlRegs.PIEIER1.bit.INTx7 = 1; // allow TIMER0 interrupt signal
    PieVectTable.TIMER0_INT = timer0_debugging_isr; // connect the isr
    EDIS;
    EINT;
    ERTM;


    Start_controller();

    CpuTimer0.RegsAddr->TCR.bit.TSS = 0; //StartCpuTimer0();

    //test_I_update(1);
    while(1){

    }
}

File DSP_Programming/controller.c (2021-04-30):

/*
 * controller.c
 *
 *  Created on: 2021. 3. 5.
 *      Author: Jaeyeon Park
 */

#include "controller.h"
#define NUM_OF_THROTTLE_MOVING_AVG_SAMPLES 10
Uint32 controlCycleCount = 0;

unsigned char adc_result_flag = 0x00;
const unsigned char ADC_ALL_SAMPLED = (FLAG_ADC_CURRENT_PHASE_U_SAMPLED
                                      |FLAG_ADC_CURRENT_PHASE_V_SAMPLED
                                      |FLAG_ADC_CURRENT_PHASE_W_SAMPLED
                                      |FLAG_ADC_THROTTLE_SAMPLED
                                      |FLAG_ADC_BATTERY_SAMPLED);


float32 offset_voltage[4] = {0, 0, 0, 0};
float32 phase_current_result[3]={0, 0, 0}; //[Ampere]
float32 dq_current_result[2] = {0,0};
float32 duty_out[3]={0,0,0};
float32 throttle_result_samples[NUM_OF_THROTTLE_MOVING_AVG_SAMPLES];
float32 throttle_result_temp_average=0;
float32 throttle_result = 0; //[Ampere]
float32 battery_level_result = 0; // 0 - 48[V]

Current_Controller CCd,CCq,CCtest;


float32 testduty0 = 0.5;
float32 testduty1 = 0.5;
float32 testduty2 = 0.5;


float32 unit_angle = 0;
float32 testangle = 0;
float32 testAlignId = 2;
float32 freq = 1;
float32 angle_E_rad=0;
float32 angular_E_speed=0;


Uint32 t_count = 0;

/****** controller constants *********/
float32 VDC = BAT_DEFAULT_VOLTAGE;
float32 CURRENT_FAULT_LIMIT = 40.0;
float32 CURRENT_LIMIT = 35.0;
byte FLAG_RUN = 0;
byte EMERGENCY_FLAG = 0;


float32* get_3phase_currents(){
    return phase_current_result;
}
float32* get_dqr_currents(){
    return dq_current_result;
}

/**********************************/
// Functions for DQ PI control with SVPWM
void Init_CC(Current_Controller* cc, float32 v_sat ){
    cc->I_ref = 0.0;
    cc->V_sat = v_sat;
    cc->V_anti = 0.0;
    cc->V_int = 0.0;
    cc->V_ref = 0.0;
    cc->V_fb = 0.0;
    cc->alpha = 1;
    cc->kp = Kp_DEFAULT;
    cc->ki = Ki_DEFAULT;
    cc->ka = Ka_DEFAULT;
    cc->kff = 0.0;
}
void abc2dq(float32 a, float32 b, float32 c, float32 angle_rad,float32* d, float32* q){
    float32 ds = a;
    float32 qs = 1/sqrt(3)*(b-c);

    float32 dr = ds*cos(angle_rad)+qs*sin(angle_rad);
    float32 qr = qs*cos(angle_rad)-ds*sin(angle_rad);

    *d = dr;
    *q = qr;

//    *d=(2.0/3.0)*( cosf(angle_rad)*a + cosf(angle_rad-2.0*PI/3.0)*b + cosf(angle_rad+2.0*PI/3.0)*c);
//    *q=(2.0/3.0)*( -sinf(angle_rad)*a - sinf(angle_rad-2.0*PI/3.0)*b - sinf(angle_rad+2.0*PI/3.0)*c);
}
void dq2abc(float32 d, float32 q, float32 angle_rad, float32* a, float32* b ,float32* c){
    *a = cos(angle_rad)*d - sin(angle_rad)*q;
    *b = cos(angle_rad - 2.0*PI/3.0)*d - sin(angle_rad - 2.0*PI/3.0)*q;
    *c = cos(angle_rad + 2.0*PI/3.0)*d - sin(angle_rad + 2.0*PI/3.0)*q;
}
float32 SVPWM_offset_voltage(float32 phase_a_v,float32 phase_b_v, float32 phase_c_v){
    float32 vmax = 0;
    float32 vmin = 0;
    if (phase_a_v > phase_b_v){
        vmax = phase_a_v;
        vmin = phase_b_v;
    }
    else{
        vmax = phase_b_v;
        vmin = phase_a_v;
    }
    if (phase_c_v > vmax){
        vmax = phase_c_v;
    }
    if (phase_c_v < vmin){
        vmin = phase_c_v;
    }
    return -(vmax+vmin)/2;
}

//
//void control_DQ(float32* phase_current,
//                Current_Controller* ccId, Current_Controller* ccIq,
//                float32 angle, float32 angular_speed,
//                float32 max_v_pole,
//                float32* duty_out){
//    // angle: rad
//    // angle_speed : rad/sec
//    float32 Ia_fb = phase_current[phaseU];
//    float32 Ib_fb = phase_current[phaseV];
//    float32 Ic_fb = phase_current[phaseW];
//    float32 Id_fb, Iq_fb;
//    float32 I_err = 0.0;
//
//    Id_fb = 0.0;
//    Iq_fb = 0.0;
//    float32 va,vb,vc, vsn, vdc, voffset_pole;
//
//    abc2dq(Ia_fb, Ib_fb, Ic_fb, angle, &Id_fb, &Iq_fb);
//
//    // control D
//    I_err = ccId->I_ref - Id_fb;
//    ccId->V_anti = ccId->V_ref - ccId->V_sat;
//    ccId->V_int += ccId->ki*(I_err - ccId->ka*ccId->V_anti);
//    ccId->V_fb = ccId->V_int + ccId->kp*I_err;
//
//    // control Q
//    I_err = ccIq->I_ref - Iq_fb;
//    ccIq->V_anti = ccIq->V_ref - ccIq->V_sat;
//    ccIq->V_int += ccIq->ki*(I_err - ccIq->ka*ccIq->V_anti);
//    ccIq->V_fb = ccIq->V_int + ccIq->kp*I_err;
//
//    ccId->V_ref = ccId->V_fb + (-Ls_DEFAULT*angular_speed*Iq_fb); // add Vd feeadforward
//    ccIq->V_ref = ccIq->V_fb + (angular_speed*Ls_DEFAULT*Id_fb + angular_speed*flux_DEFAULT); // Vq feedforward
//
//    dq2abc(ccId->V_ref, ccIq->V_ref, angle, &va, &vb, &vc);
//    vsn = SVPWM_offset_voltage(va,vb,vc);
//
//    vdc = max_v_pole;
//    voffset_pole = vdc/2;
//
//    vsn += voffset_pole;
//
//    va += vsn;
//    vb += vsn;
//    vc += vsn;
//
//    va = (va > vdc) ? vdc : ((va < 0)? 0: va);
//    vb = (vb > vdc) ? vdc : ((vb < 0)? 0: vb);
//    vc = (vc > vdc) ? vdc : ((vc < 0)? 0: vc);
//
//    duty_out[phaseU] = va/vdc;
//    duty_out[phaseV] = vb/vdc;
//    duty_out[phaseW] = vc/vdc;
//
//}
//void control_sinusoidal_BEMF(){
//    float32 duty[3]={0,0,0};
//    float32 angle = hall_sensor_get_E_angle_rad();
//    float32 angular_speed = hall_sensor_get_E_angular_speed();   //0; // TODO update needed
//
//    // calculate Iabc->DQ->PI->DQ->Vabc
//    control_DQ(phase_current_result,
//               &CCd, &CCq, angle, angular_speed,
//               BAT_DEFAULT_VOLTAGE,
//               duty);
//
//
//    epwm1_set_duty(duty[phaseU], 1-duty[phaseU]);
//    epwm2_set_duty(duty[phaseV], 1-duty[phaseV]);
//    epwm3_set_duty(duty[phaseW], 1-duty[phaseW]);
//}
/*************TEST CODE******************/
void test_angle_update(float32 unit_angle){
    testangle += unit_angle;
    if(testangle >= 2*PI){
        testangle = 0;
    }else if(testangle <= -2*PI){
        testangle = 0;
    }
}
void test_Idq_update(float32 Id_ref, float32 Iq_ref){
    CCd.I_ref = Id_ref;
    CCq.I_ref = Iq_ref;
}
void test_I_update(float32 current){CCtest.I_ref = current;}
void test_poll_voltage(float32 duty){
    // 폴 전압이 원하는 듀티로 잘 변경되고 있음을 확인함.
    epwm1_set_duty(testduty0, 1-testduty0);
    epwm2_set_duty(testduty1, 1-testduty1);
    epwm3_set_duty(testduty2, 1-testduty2);
}

//void test_V_DQ(float32 vdr, float32 vqr, float32 angle_rad, float32 vdc){
//    // 3상 DQ 변환이 잘 제어되고 있음을 확인함
//
//    float32 va, vb, vc, vsn;
//
//    dq2abc(vdr,vqr,angle_rad, &va, &vb, &vc);
//    vsn = SVPWM_offset_voltage(va,vb,vc);
//    va += (vsn+24);
//    vb += (vsn+24);
//    vc += (vsn+24);
//
//    va = (va > vdc) ? vdc : ((va < 0)? 0: va);
//    vb = (vb > vdc) ? vdc : ((vb < 0)? 0: vb);
//    vc = (vc > vdc) ? vdc : ((vc < 0)? 0: vc);
//
//    duty_out[phaseU] = va/vdc;
//    duty_out[phaseV] = vb/vdc;
//    duty_out[phaseW] = vc/vdc;
//
//    epwm1_set_duty(duty_out[phaseU], 1-duty_out[phaseU]);
//    epwm2_set_duty(duty_out[phaseV], 1-duty_out[phaseV]);
//    epwm3_set_duty(duty_out[phaseW], 1-duty_out[phaseW]);
//}
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

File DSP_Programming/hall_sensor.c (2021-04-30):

/*
 * hall_sensor2.c
 *
 *  Created on: 2021. 3. 12.
 *      Author: ok6530
 */

#include <hall_sensor.h>

#define POLE_PAIR 23
#define BOUND_PI(x)      ((x) - TWOPI * floor(((x) + PI) * INV_TWOPI))

Hall_state prev_state;
Hall_state hall_state;
Angle_observer angle_observer;

float32 time1=0;
Uint32 t_counter = 0;
float32 update_period = 1/10e3;

Hall_state get_hall_state(){
    return hall_state;
}

void Init_hall_sensor(){

    EALLOW;
    // H_U
    GpioCtrlRegs.GPBGMUX2.bit.GPIO60 = 0; // use GPIO60 as gpio
    GpioCtrlRegs.GPBMUX2.bit.GPIO60 = 0;
    GpioCtrlRegs.GPBDIR.bit.GPIO60 = 0; // GPIO FOR INPUT
    GpioCtrlRegs.GPBQSEL2.bit.GPIO60 = 0x0; // Input Qualification type - Sync
    GpioCtrlRegs.GPBPUD.bit.GPIO60 = 0; // PULL UP
    // H_V
    GpioCtrlRegs.GPAGMUX2.bit.GPIO22 = 0;
    GpioCtrlRegs.GPAMUX2.bit.GPIO22 = 0;
    GpioCtrlRegs.GPADIR.bit.GPIO22 = 0;
    GpioCtrlRegs.GPAQSEL2.bit.GPIO22 = 0x0;
    GpioCtrlRegs.GPAPUD.bit.GPIO22 = 0;
    // H_W
    GpioCtrlRegs.GPDGMUX1.bit.GPIO105 = 0;
    GpioCtrlRegs.GPDMUX1.bit.GPIO105 = 0;
    GpioCtrlRegs.GPDDIR.bit.GPIO105 = 0;
    GpioCtrlRegs.GPDQSEL1.bit.GPIO105 = 0X0;
    GpioCtrlRegs.GPDPUD.bit.GPIO105 = 0;
}
void Start_hall_sensor(){
    hall_state = hall_sensor_update(); // Get initial state
    prev_state = hall_state;

    //start_ecap

    EINT;
}

Angle_observer get_angle_observer(){
    return angle_observer;
}

void Init_angle_observer(){
    angle_observer.Kp = ANGLE_OBSERVER_KP;
    angle_observer.Ki = ANGLE_OBSERVER_KI;
    angle_observer.Wr = 0.0;
    angle_observer.angle = 0.0;
}

float32 angle_observer_update(float32 hall_sensor_angle){
    float32 angle_err = BOUND_PI(hall_sensor_angle - angle_observer.angle);
    angle_observer.Wr+= angle_observer.Ki*angle_err*update_period;
    angle_observer.angle += (angle_observer.Wr + angle_observer.Kp*angle_err)*update_period;
    angle_observer.angle = BOUND_PI(angle_observer.angle);
    return angle_observer.angle;
}

float32 calibrate_angle_offset(float32 angle){
    return BOUND_PI(angle - hall_state.angle_E_offset_rad);
}


Hall_state hall_sensor_update(){ // Hwigon Kim
    Hall_state state;

    state.hu = GpioDataRegs.GPBDAT.bit.GPIO60;
    state.hv = GpioDataRegs.GPADAT.bit.GPIO22;
    state.hw = GpioDataRegs.GPDDAT.bit.GPIO105;
    state.angle_E_offset_rad = 4.5; //PI/3;

    if(state.hu & !state.hv & state.hw){
        // 1 0 1
        // 5*pi/3 - 6*pi/3
        hall_state.angle_E_rad = 5*Deg_60_IN_RAD;
    }else if(state.hu & !state.hv & !state.hw){
        // 1 0 0
        // 0 - pi/3
        hall_state.angle_E_rad = 0;
    }else if(state.hu & state.hv & !state.hw){
        // 1 1 0
        // pi/3 - 2*pi/3
        hall_state.angle_E_rad = Deg_60_IN_RAD;
    }else if(!state.hu & state.hv & !state.hw){
        // 0 1 0
        // 2*pi/3 - 3*pi/3
        hall_state.angle_E_rad = 2*Deg_60_IN_RAD;
    }else if(!state.hu & state.hv & state.hw){
        // 0 1 1
        // 3*pi/3 - 4*pi/3
        hall_state.angle_E_rad = 3*Deg_60_IN_RAD;
    }else if(!state.hu & !state.hv & state.hw){
        // 0 0 1
        // 4*pi/3 - 5*pi/3
        hall_state.angle_E_rad = 4*Deg_60_IN_RAD;
    }else{
        hall_state.angle_E_rad = state.angle_E_offset_rad;
    }
    hall_state.angle_E_rad = BOUND_PI(hall_state.angle_E_rad);



    if(state.hu != hall_state.hu ||
       state.hv != hall_state.hv ||
       state.hw != hall_state.hw){
       state.Wr = PI/3.0/(t_counter*update_period);
       hall_state.Wr = state.Wr;
       t_counter = 0;
       hall_state.hu = state.hu;
       hall_state.hv = state.hv;
       hall_state.hw = state.hw;
    }else if(t_counter >= 1.0/update_period){
        hall_state.Wr = 0;
        state.Wr = 0;
        t_counter = 0;
    }else{
        t_counter++;
    }

    return state;
}

void hall_sensor_set_angle_offset_rad(float64 offset_rad){
    hall_state.angle_E_offset_rad = offset_rad;
}

float64 hall_sensor_get_E_angle_rad(){
    float64 time2 = ECap1Regs.TSCTR;
    float64 angle;
    angle = hall_state.angle_E_rad + (t_counter*update_period)*hall_state.Wr;
    if (angle > hall_state.angle_E_rad+PI/3.0){
        angle = hall_state.angle_E_rad+PI/3.0;
    }
    if (angle < hall_state.angle_E_rad-PI/3.0){
        angle = hall_state.angle_E_rad-PI/3.0;
    }

    return (BOUND_PI(angle));
}

float64 hall_sensor_get_E_angular_speed(){
    return hall_state.Wr;
}
float64 hall_sensor_get_M_angular_speed(){
    return hall_state.Wr/POLE_PAIR;
}

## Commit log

2021-03-03 apply real gpio pin for hall sensors
2021-03-03 fix the change in carrier wave from pwm pn & sync the counter in eCAP
    [hall_sensor.c, hall_sensor.h, main.c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]
2021-03-04 sync hall sensor and ePWM
2021-03-04 fix the varied frequency bug in ePWM
    the carrier frequency of ePWM is varied because of the external sync source or some other sources.
    solution : disable PHSEN bit like this
    ePWM.TBCTL.bit.PHSEN = 0
    [hall_sensor.c, main.c, pwm_run.c]
2021-03-04 add pwm testcode
2021-03-04 add ADC and connect EPWMxSOCA <-> ADC
2021-03-04 ADC complete (throttle and battery)
2021-03-04 ePWMxSOCB triggers throttle ADC conversion
2021-03-04 adc sampilng에 대한 설명 변경
2021-03-05 connect control_function to call after completing ADC Sample&Hold and conversion
2021-03-08 Kp, Ki fixed
    update coefficient for PI controller with Anti windup
    update control motor having trapezoidal back EMF pulse shape
    [controller.c, hall_sensor.c, hall_sensor.h]
2021-03-09 fix wrong phase flag
    [adc_current.c]
2021-03-09 fix dumb epwm AQCTLB
    [controller.c, pwm_run.c]
2021-03-09 fix dumb mistake about PWM
    [controller.c, pwm_run.c]
2021-03-11 add comments to hall sensor
2021-03-11 fix inverted pwm output
    [pwm_run.c]
2021-03-11 add indicator led
2021-03-16 add initila adc sampling to measure offset voltage
2021-03-16 ADD HALL SENSOR ANGLE UPDATE & change throttle ADCIN to 5 from 4
2021-03-18 change ADC channel
2021-03-23 integrate hall sensor
2021-04-02 change duty and comment for pwm
2021-04-07 fix initial ePWM duty configuration
    [controller.c, main.c, pwm_run.c]
2021-04-08 save me
    1. epwm sync fixed
    2. right before Vector Current Control
    [controller.c, hall_sensor.c, hall_sensor.h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]
2021-04-08 fix zubbul
    hate disconnected wire
    [controller.c]
2021-04-08 fix angle_E_rad not updated
    [controller.c]
2021-04-08 fix integer division problem
    [hall_sensor.c]
2021-04-10 linear interpolation hall sensor
2021-04-19 change max iq command current
2021-04-27 change current sensor(wcs1700) that has -70A to 70A current range
2021-04-27 change to max current 35A
2021-04-29 phase W is wrong
    [controller.c]
2021-04-30 750W motor
2021-06-20 add PCB schematics
    [inverter_4layer_IPM(mouser).xlsx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]
2021-08-20 FIX MISINFORMATION ABOUT POWER SWITCH
    NFAL5065L4B is not the mosfet switch, it is IGBT switchi
